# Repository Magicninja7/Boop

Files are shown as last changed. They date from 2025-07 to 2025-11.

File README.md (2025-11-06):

Description: Its a polar, 4axis, cantivileerian 3d printer! It uses a unorthodox aproach to rotate the hotend in b axis, and y axis, using only 2 motors and being pretty cool! The printbed is also backlit!! :3
WHy? idk, felt like it tbh. Saw a cool video on yt, thought: i wanna do that. And then highway happened. And then this happened.

## Cad 
looks kinda sick ngl

## PCB
this took more time than you think

## Diagram

Power Supply (LRS-350-24) Connections

LRS-350-24:

    AC Input L (Live): → Mains AC Hot
    AC Input N (Neutral): → Mains AC Neutral
    AC Input Ground: → Mains AC Ground
    +V (24V): → SKR3 VIN terminal
    -V (Ground): → SKR3 GND terminal
    +V (24V): → LED Strip positive terminal
    -V (Ground): → LED Strip negative terminal

SKR3 Main Board Connections
Stepper Motor Drivers

SKR3:

    Driver Socket X: → X-axis stepper driver (TMC2209/TMC2226)
    Driver Socket Y: → Y-axis stepper driver (TMC2209/TMC2226)
    Driver Socket Z: → Z-axis stepper driver (TMC2209/TMC2226)
    Driver Socket E0: → Extruder stepper driver (TMC2209/TMC2226)

Endstop Switches

SKR3:

    X-STOP pin 1 (Signal): → X endstop switch NO (Normally Open)
    X-STOP pin 2 (GND): → X endstop switch COM (Common)
    Y-STOP pin 1 (Signal): → Y endstop switch NO (Normally Open)
    Y-STOP pin 2 (GND): → Y endstop switch COM (Common)
    Z-STOP pin 1 (Signal): → Z endstop switch NO (Normally Open)
    Z-STOP pin 2 (GND): → Z endstop switch COM (Common)

Hotend (XC1) Connections

SKR3:

    HE0 pin 1 (+): → XC1 hotend heater cartridge positive
    HE0 pin 2 (-): → XC1 hotend heater cartridge negative
    TH0 pin 1 (Signal): → B57560G1104F000 thermistor pin 1
    TH0 pin 2 (GND): → B57560G1104F000 thermistor pin 2
    FAN0 pin 1 (+): → XC1 cooling fan positive (24V)
    FAN0 pin 2 (-): → XC1 cooling fan negative

Print Bed Connections

SKR3:

    HE1/BED pin 1 (+): → Print bed heater positive
    HE1/BED pin 2 (-): → Print bed heater negative
    THB pin 1 (Signal): → Bed thermistor positive (if separate)
    THB pin 2 (GND): → Bed thermistor negative (if separate)

LED Strip Connections

SKR3:

    FAN1 pin 1 (+): → LED strip positive (via MOSFET if needed)
    FAN1 pin 2 (-): → LED strip negative

## Parts

| Part | Qty | total$ | link |
| ---- | --- | ----- | ---- |
| sherpa mini | 1 | 24 | [Ali](https://pl.aliexpress.com/item/1005002487727392.html?gatewayAdapt=glo2pol) |
| vslot rail | 2 | 16 | [Ali](https://pl.aliexpress.com/i/1005003311298946.html?gatewayAdapt=glo2pol)
| nema17+screw | 2 | 20 | [Ali](https://pl.aliexpress.com/item/1005005575285492.html?gatewayAdapt=usa2pol)
| nema17 | 3 | 15 | [Ali](https://pl.aliexpress.com/item/1005003874936862.html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)
| skr3+drivers | 1 | 77 | [Ali](https://www.aliexpress.com/item/1005007540045155.html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)
| lrs-350-24 | 1 | 35 | [Ali](https://www.aliexpress.com/item/1005006104414563.html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)
| pillow-bearing | 2 | 12 | [Ali](https://pl.aliexpress.com/item/1005008115694493.html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)
| pulley | 2 | 3 | [Ali](https://www.aliexpress.us/item/1005004314084512.html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)
| pulley no-teeth | 4 | 12 | [Ali](https://www.aliexpress.us/item/1005004314084512.html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)
| back-pulley-xaxis | 1 | 2 | [Ali](https://www.aliexpress.us/item/32817328238.html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)
| big-xaxis-pulley | 1 | 5 | [Ali](https://www.fallshaw.com.au/products/SPBRGQ6004X20)
| bearing-uni | 4 | 5 | [Ali](https://modelemax.pl/en/bearings/19394-ball-bearing-8-24-8mm-628zz)
| gantry_vslot | 2 | 18 | [Ali](https://pl.aliexpress.com/item/4000252044823.html?gatewayAdapt=glo2pol)
| 4010 fan | 1 | 4 | [Ali](https://pl.aliexpress.com/item/1005003462239029.html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)
| sliding rod | 1 | 3.2 | [ali](https://pl.aliexpress.com/item/1005006293171727.html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)
| lm8uu bearing | 2 | 3 | [ali](https://pl.aliexpress.com/item/1005007070280422.html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)
| m4 screws+nuts | 36 | 8 | local_shop
| m3 screws+nuts | 25 | 8 | local_shop
| m2 wcrews+nutss | 4 | 1 | local_shop
| m2.5 screw | 2 | 1 | local_shop
| m5 screws+nuts | 35 | 4 | local_shop
| m8 screws+nuts | 5 | 4 | local_shop
| B57560G1104F000 thermistor | 2 | 8 | [mouser](https://eu.mouser.com/ProductDetail/EPCOS-TDK/B57560G1104F000?qs=%2FsLciWRBLmAyaJsNOAuWiw%3D%3D)
| leds4printbed | 75 | 15 | [piekarz🔥](https://www.piekarz.pl/37911-dioda-led-worldsemi-ws2812b-v4/)
| gt2 belt | 1 | 8 | [Ali](https://www.aliexpress.us/item/10000115962505.html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)
| nutblock | 2 | 6 | [Ali](https://pl.aliexpress.com/item/1005004033091930.html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) 
| xc1 hotend | 1 | 2 | [Ali](https://pl.aliexpress.com/item/1005007319888761.html)
| jumper cables (m2m & f2f & m2f) | 40 each | 8 | [Botland](https://botland.com.pl/przewody-polaczeniowe-zensko-meskie/19621-zestaw-przewodow-polaczeniowych-justpi-zensko-meskie-20cm-40szt-5903351243025.html) note: after customs aliexpress is actually more expensive + m2m and f2f connectors cost the same - ~2.5$)
| endstop switches | 3 | 4 | [ali](https://pl.aliexpress.com/item/1005008640444653.html)  
| pcb | 1 | 20 | [jlcpcb](https://jlcpcb.com/)

holy fuck 
its actually exactly 350$ 
wtf
nicee
i though i was gonna pay from pocket

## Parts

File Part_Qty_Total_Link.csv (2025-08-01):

Part | Qty | Total | Link
sherpa mini | 1 | 34 | https://pl.aliexpress.com/item/1005002487727392.html
vslot rail | 2 | 16 | https://pl.aliexpress.com/i/1005003311298946.html?gatewayAdapt=glo2pol
nema17+screw | 1 | 50 | https://www.aliexpress.us/item/1005005575285492.html?mp=1&gatewayAdapt=glo2usa
nema17 | 3 | 44 | https://www.aliexpress.us/item/1005007721263858.html?pdp
skr3+drivers | 1 | 77 | https://www.aliexpress.com/item/1005007540045155.html
lrs-350-24 | 1 | 35 | https://www.aliexpress.com/item/1005006104414563.html
pillow-bearing | 2 | 12 | https://pl.aliexpress.com/item/1005008115694493.html?pd
pulley | 2 | 3 | https://www.aliexpress.us/item/1005004314084512.html
pulley no-teeth | 4 | 12 | https://www.aliexpress.us/item/1005004314084512.html
back-pulley-xaxis | 1 | 2 | https://www.aliexpress.us/item/32817328238.html
big-xaxis-pulley | 1 | 5 | https://www.fallshaw.com.au/products/SPBRGQ6004X20
bearing-uni | 4 | 5 | https://modelemax.pl/en/bearings/19394-ball-bearing-8-24-8mm-628zz
gantry_vslot | 2 | 18 | https://pl.aliexpress.com/item/4000252044823.html?gatewayAdapt=glo2pol
4010 fan | 1 | 4 | https://pl.aliexpress.com/item/1005003462239029.html?pdp_ext_f
sliding rod | 1 | 23 | https://pl.aliexpress.com/item/1005006293171727.html?pdp_e
lm8uu bearing | 2 | 3 | https://pl.aliexpress.com/item/1005007070280422.html
m4 screws+nuts | 36 | 8 | local_shop
m3 screws+nuts | 25 | 8 | local_shop
m2 wcrews+nutss | 4 | 1 | local_shop
m2.5 screw | 2 | 1 | local_shop
m5 screws+nuts | 35 | 4 | local_shop
m8 screws+nuts | 5 | 4 | local_shop
B57560G1104F000 thermistor | 2 | 8 | https://eu.mouser.com/ProductDetail/EPCOS-TDK/B57560G1104F000?qs=%2FsLciWRBLmAyaJsNOAuWiw%3D%3D
leds4printbed | 75 | 15 | https://www.piekarz.pl/37911-dioda-led-worldsemi-ws2812b-v4/
gt2 belt | 1 | 8 | https://www.aliexpress.us/item/10000115962505.html?pdp_
nutblock | 2 | 6 | https://pl.aliexpress.com/item/1005004033091930.html?pdp_ext_
xc1 hotend | 1 | 2 | https://pl.aliexpress.com/item/1005007319888761.html
jumper cables (m2m & f2f & m2f) | 40 each | 8 | https://botland.com.pl/przewody-polaczeniowe-zensko-meskie/19621-zestaw-przewodow-polaczeniowych-justpi-zensko-meskie-20cm-40szt-590335
endstop switches | 3 | 4 | https://pl.aliexpress.com/item/1005008640444653.html
pcb | 1 | 50 | https://jlcpcb.com/

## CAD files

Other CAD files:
Main_v58.f3z

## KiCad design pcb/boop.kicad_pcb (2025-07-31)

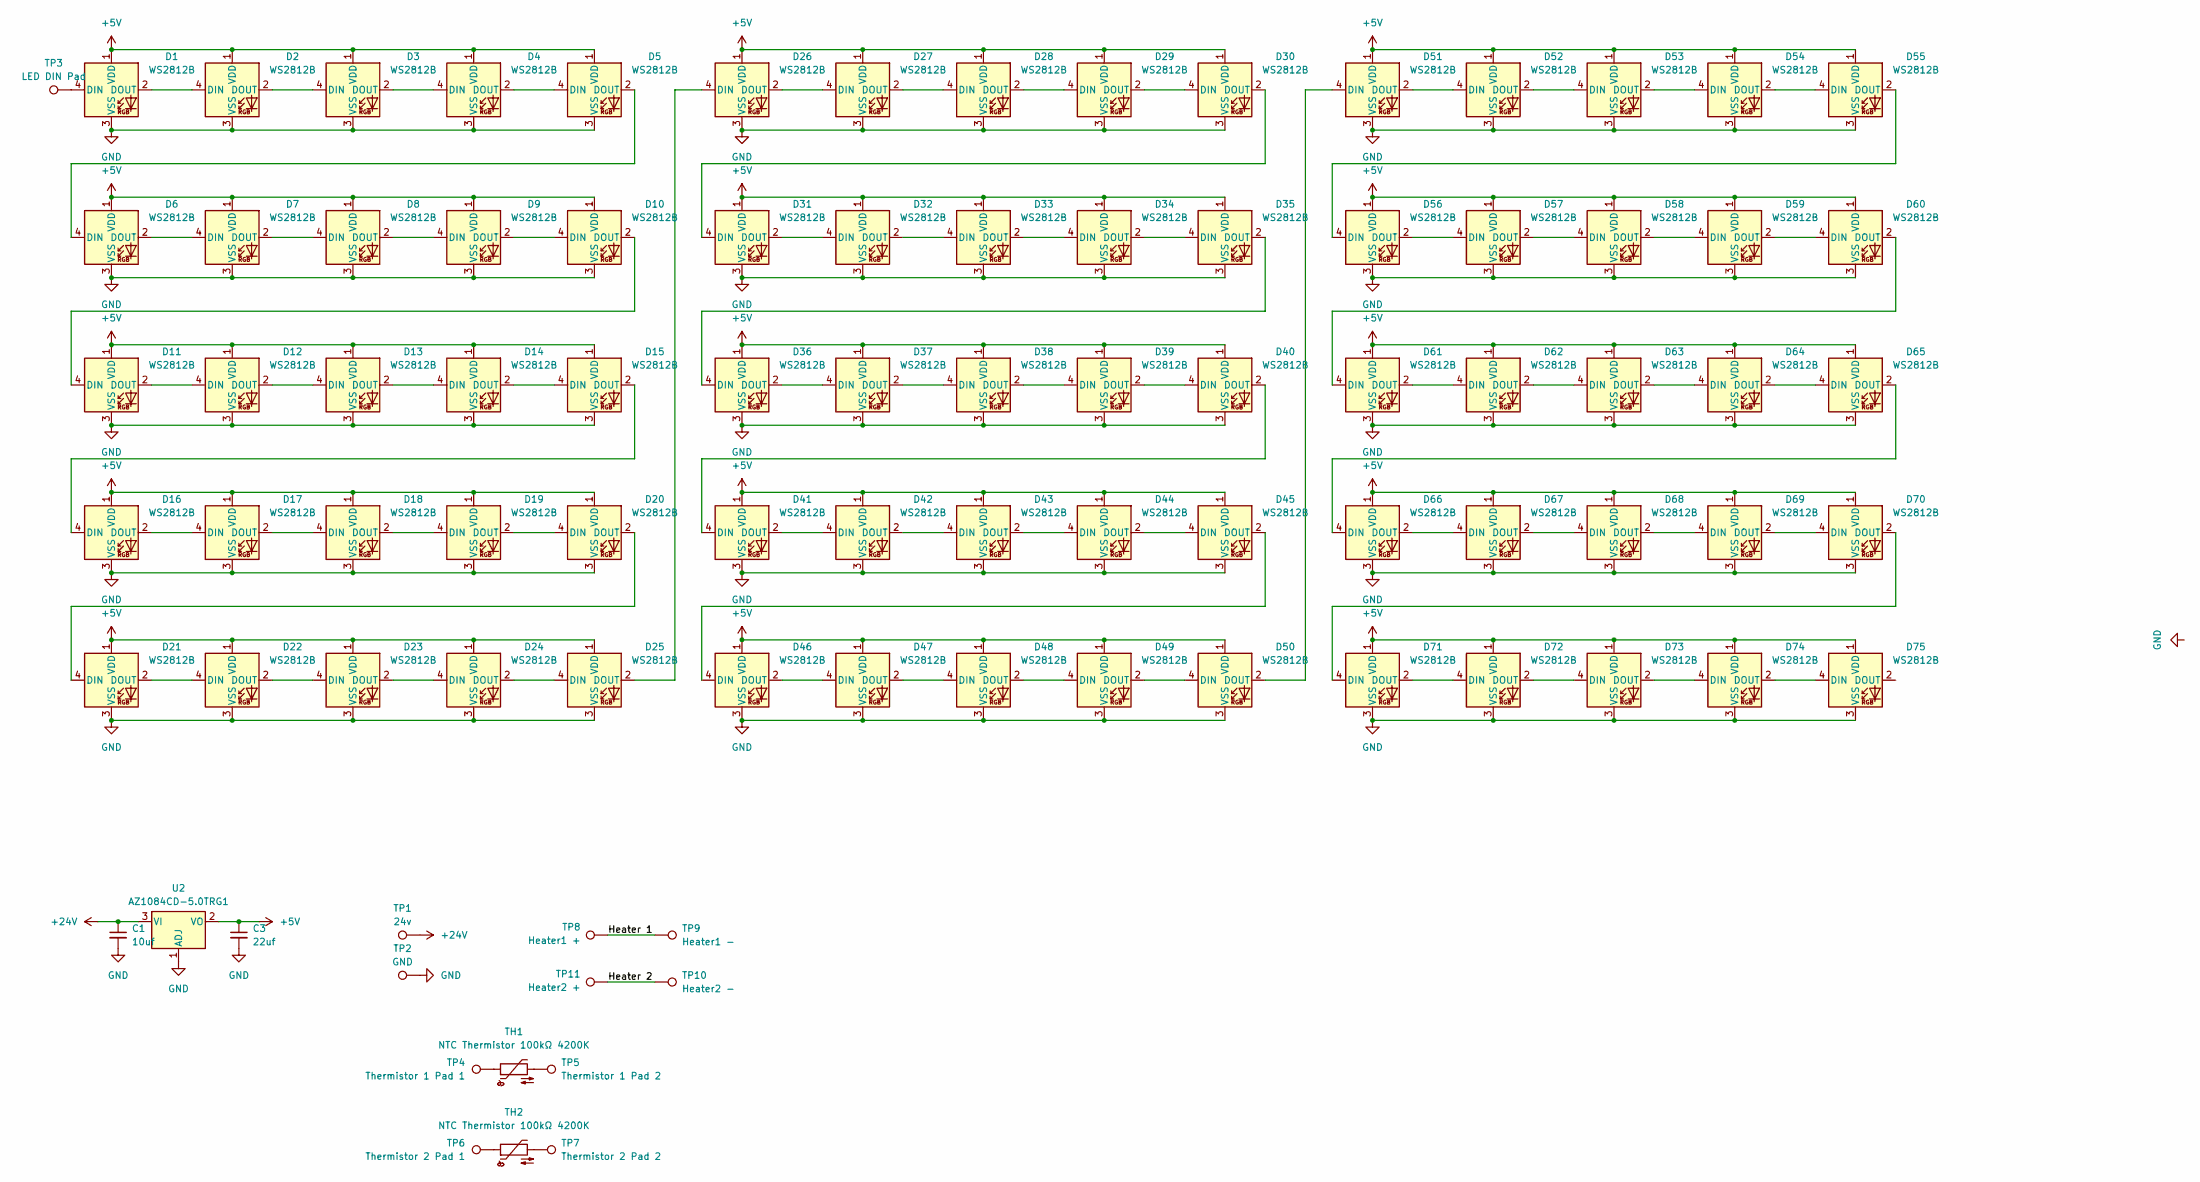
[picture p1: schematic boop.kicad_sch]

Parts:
C1: 10uf
C3: 22uf
D1, D2, D3, D4, D5, D6, D7, D8, D9, D10, D11, D12, D13, D14, D15, D16, D17, D18, D19, D20, D21, D22, D23, D24, D25, D26, D27, D28, D29, D30, D31, D32, D33, D34, D35, D36, D37, D38, D39, D40, D41, D42, D43, D44, D45, D46, D47, D48, D49, D50, D51, D52, D53, D54, D55, D56, D57, D58, D59, D60, D61, D62, D63, D64, D65, D66, D67, D68, D69, D70, D71, D72, D73, D74, D75: WS2812B; LED_WS2812B_PLCC4_5.0x5.0mm_P3.2mm
TH1, TH2: NTC Thermistor 100kΩ 4200K; R_0805_2012Metric_Pad1.20x1.40mm_HandSolder
TP1: 24v; TestPoint_Pad_4.0x4.0mm
TP2: GND; TestPoint_Pad_4.0x4.0mm
TP3: LED DIN Pad; TestPoint_Pad_2.5x2.5mm
TP4: Thermistor 1 Pad 1; TestPoint_Pad_2.0x2.0mm
TP5: Thermistor 1 Pad 2; TestPoint_Pad_2.0x2.0mm
TP6: Thermistor 2 Pad 1; TestPoint_Pad_2.0x2.0mm
TP7: Thermistor 2 Pad 2; TestPoint_Pad_2.0x2.0mm
TP8: Heater1 +; TestPoint_Pad_4.0x4.0mm
TP9: Heater1 -; TestPoint_Pad_4.0x4.0mm
TP10: Heater2 -; TestPoint_Pad_4.0x4.0mm
TP11: Heater2 +; TestPoint_Pad_4.0x4.0mm
U2: AZ1084CD-5.0TRG1; TO-252-2

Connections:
+5V: C3.1, D1.1 (VDD), D2.1 (VDD), D3.1 (VDD), D4.1 (VDD), D5.1 (VDD), D6.1 (VDD), D7.1 (VDD), D8.1 (VDD), D9.1 (VDD), D10.1 (VDD), D11.1 (VDD), D12.1 (VDD), D13.1 (VDD), D14.1 (VDD), D15.1 (VDD), D16.1 (VDD), D17.1 (VDD), D18.1 (VDD), D19.1 (VDD), D20.1 (VDD), D21.1 (VDD), D22.1 (VDD), D23.1 (VDD), D24.1 (VDD), D25.1 (VDD), D26.1 (VDD), D27.1 (VDD), D28.1 (VDD), D29.1 (VDD), D30.1 (VDD), D31.1 (VDD), D32.1 (VDD), D33.1 (VDD), D34.1 (VDD), D35.1 (VDD), D36.1 (VDD), D37.1 (VDD), D38.1 (VDD), D39.1 (VDD), D40.1 (VDD), D41.1 (VDD), D42.1 (VDD), D43.1 (VDD), D44.1 (VDD), D45.1 (VDD), D46.1 (VDD), D47.1 (VDD), D48.1 (VDD), D49.1 (VDD), D50.1 (VDD), D51.1 (VDD), D52.1 (VDD), D53.1 (VDD), D54.1 (VDD), D55.1 (VDD), D56.1 (VDD), D57.1 (VDD), D58.1 (VDD), D59.1 (VDD), D60.1 (VDD), D61.1 (VDD), D62.1 (VDD), D63.1 (VDD), D64.1 (VDD), D65.1 (VDD), D66.1 (VDD), D67.1 (VDD), D68.1 (VDD), D69.1 (VDD), D70.1 (VDD), D71.1 (VDD), D72.1 (VDD), D73.1 (VDD), D74.1 (VDD), D75.1 (VDD), U2.2 (VO)
+24V: C1.1, TP1.1, U2.3 (VI)
/Heater 1: TP8.1, TP9.1
/Heater 2: TP10.1, TP11.1
GND: C1.2, C3.2, D1.3 (VSS), D2.3 (VSS), D3.3 (VSS), D4.3 (VSS), D5.3 (VSS), D6.3 (VSS), D7.3 (VSS), D8.3 (VSS), D9.3 (VSS), D10.3 (VSS), D11.3 (VSS), D12.3 (VSS), D13.3 (VSS), D14.3 (VSS), D15.3 (VSS), D16.3 (VSS), D17.3 (VSS), D18.3 (VSS), D19.3 (VSS), D20.3 (VSS), D21.3 (VSS), D22.3 (VSS), D23.3 (VSS), D24.3 (VSS), D25.3 (VSS), D26.3 (VSS), D27.3 (VSS), D28.3 (VSS), D29.3 (VSS), D30.3 (VSS), D31.3 (VSS), D32.3 (VSS), D33.3 (VSS), D34.3 (VSS), D35.3 (VSS), D36.3 (VSS), D37.3 (VSS), D38.3 (VSS), D39.3 (VSS), D40.3 (VSS), D41.3 (VSS), D42.3 (VSS), D43.3 (VSS), D44.3 (VSS), D45.3 (VSS), D46.3 (VSS), D47.3 (VSS), D48.3 (VSS), D49.3 (VSS), D50.3 (VSS), D51.3 (VSS), D52.3 (VSS), D53.3 (VSS), D54.3 (VSS), D55.3 (VSS), D56.3 (VSS), D57.3 (VSS), D58.3 (VSS), D59.3 (VSS), D60.3 (VSS), D61.3 (VSS), D62.3 (VSS), D63.3 (VSS), D64.3 (VSS), D65.3 (VSS), D66.3 (VSS), D67.3 (VSS), D68.3 (VSS), D69.3 (VSS), D70.3 (VSS), D71.3 (VSS), D72.3 (VSS), D73.3 (VSS), D74.3 (VSS), D75.3 (VSS), TP2.1, U2.1 (ADJ)
unnamed: D1.4 (DIN), TP3.1
unnamed: D1.2 (DOUT), D2.4 (DIN)
unnamed: D2.2 (DOUT), D3.4 (DIN)
unnamed: D3.2 (DOUT), D4.4 (DIN)
unnamed: D4.2 (DOUT), D5.4 (DIN)
unnamed: D5.2 (DOUT), D6.4 (DIN)
unnamed: D6.2 (DOUT), D7.4 (DIN)
unnamed: D7.2 (DOUT), D8.4 (DIN)
unnamed: D8.2 (DOUT), D9.4 (DIN)
unnamed: D9.2 (DOUT), D10.4 (DIN)
unnamed: D10.2 (DOUT), D11.4 (DIN)
unnamed: D11.2 (DOUT), D12.4 (DIN)
unnamed: D12.2 (DOUT), D13.4 (DIN)
unnamed: D13.2 (DOUT), D14.4 (DIN)
unnamed: D14.2 (DOUT), D15.4 (DIN)
unnamed: D15.2 (DOUT), D16.4 (DIN)
unnamed: D16.2 (DOUT), D17.4 (DIN)
unnamed: D17.2 (DOUT), D18.4 (DIN)
unnamed: D18.2 (DOUT), D19.4 (DIN)
unnamed: D19.2 (DOUT), D20.4 (DIN)
unnamed: D20.2 (DOUT), D21.4 (DIN)
unnamed: D21.2 (DOUT), D22.4 (DIN)
unnamed: D22.2 (DOUT), D23.4 (DIN)
unnamed: D23.2 (DOUT), D24.4 (DIN)
unnamed: D24.2 (DOUT), D25.4 (DIN)
unnamed: D25.2 (DOUT), D26.4 (DIN)
unnamed: D26.2 (DOUT), D27.4 (DIN)
unnamed: D27.2 (DOUT), D28.4 (DIN)
unnamed: D28.2 (DOUT), D29.4 (DIN)
unnamed: D29.2 (DOUT), D30.4 (DIN)
unnamed: D30.2 (DOUT), D31.4 (DIN)
unnamed: D31.2 (DOUT), D32.4 (DIN)
unnamed: D32.2 (DOUT), D33.4 (DIN)
unnamed: D33.2 (DOUT), D34.4 (DIN)
unnamed: D34.2 (DOUT), D35.4 (DIN)
unnamed: D35.2 (DOUT), D36.4 (DIN)
unnamed: D36.2 (DOUT), D37.4 (DIN)
unnamed: D37.2 (DOUT), D38.4 (DIN)
unnamed: D38.2 (DOUT), D39.4 (DIN)
unnamed: D39.2 (DOUT), D40.4 (DIN)
unnamed: D40.2 (DOUT), D41.4 (DIN)
unnamed: D41.2 (DOUT), D42.4 (DIN)
unnamed: D42.2 (DOUT), D43.4 (DIN)
unnamed: D43.2 (DOUT), D44.4 (DIN)
unnamed: D44.2 (DOUT), D45.4 (DIN)
unnamed: D45.2 (DOUT), D46.4 (DIN)
unnamed: D46.2 (DOUT), D47.4 (DIN)
unnamed: D47.2 (DOUT), D48.4 (DIN)
unnamed: D48.2 (DOUT), D49.4 (DIN)
unnamed: D49.2 (DOUT), D50.4 (DIN)
unnamed: D50.2 (DOUT), D51.4 (DIN)
unnamed: D51.2 (DOUT), D52.4 (DIN)
unnamed: D52.2 (DOUT), D53.4 (DIN)
unnamed: D53.2 (DOUT), D54.4 (DIN)
unnamed: D54.2 (DOUT), D55.4 (DIN)
unnamed: D55.2 (DOUT), D56.4 (DIN)
unnamed: D56.2 (DOUT), D57.4 (DIN)
unnamed: D57.2 (DOUT), D58.4 (DIN)
unnamed: D58.2 (DOUT), D59.4 (DIN)
unnamed: D59.2 (DOUT), D60.4 (DIN)
unnamed: D60.2 (DOUT), D61.4 (DIN)
unnamed: D61.2 (DOUT), D62.4 (DIN)
unnamed: D62.2 (DOUT), D63.4 (DIN)
unnamed: D63.2 (DOUT), D64.4 (DIN)
unnamed: D64.2 (DOUT), D65.4 (DIN)
unnamed: D65.2 (DOUT), D66.4 (DIN)
unnamed: D66.2 (DOUT), D67.4 (DIN)
unnamed: D67.2 (DOUT), D68.4 (DIN)
unnamed: D68.2 (DOUT), D69.4 (DIN)
unnamed: D69.2 (DOUT), D70.4 (DIN)
unnamed: D70.2 (DOUT), D71.4 (DIN)
unnamed: D71.2 (DOUT), D72.4 (DIN)
unnamed: D72.2 (DOUT), D73.4 (DIN)
unnamed: D73.2 (DOUT), D74.4 (DIN)
unnamed: D74.2 (DOUT), D75.4 (DIN)
unnamed: TH1.1, TP4.1
unnamed: TH1.2, TP5.1
unnamed: TH2.1, TP6.1
unnamed: TH2.2, TP7.1

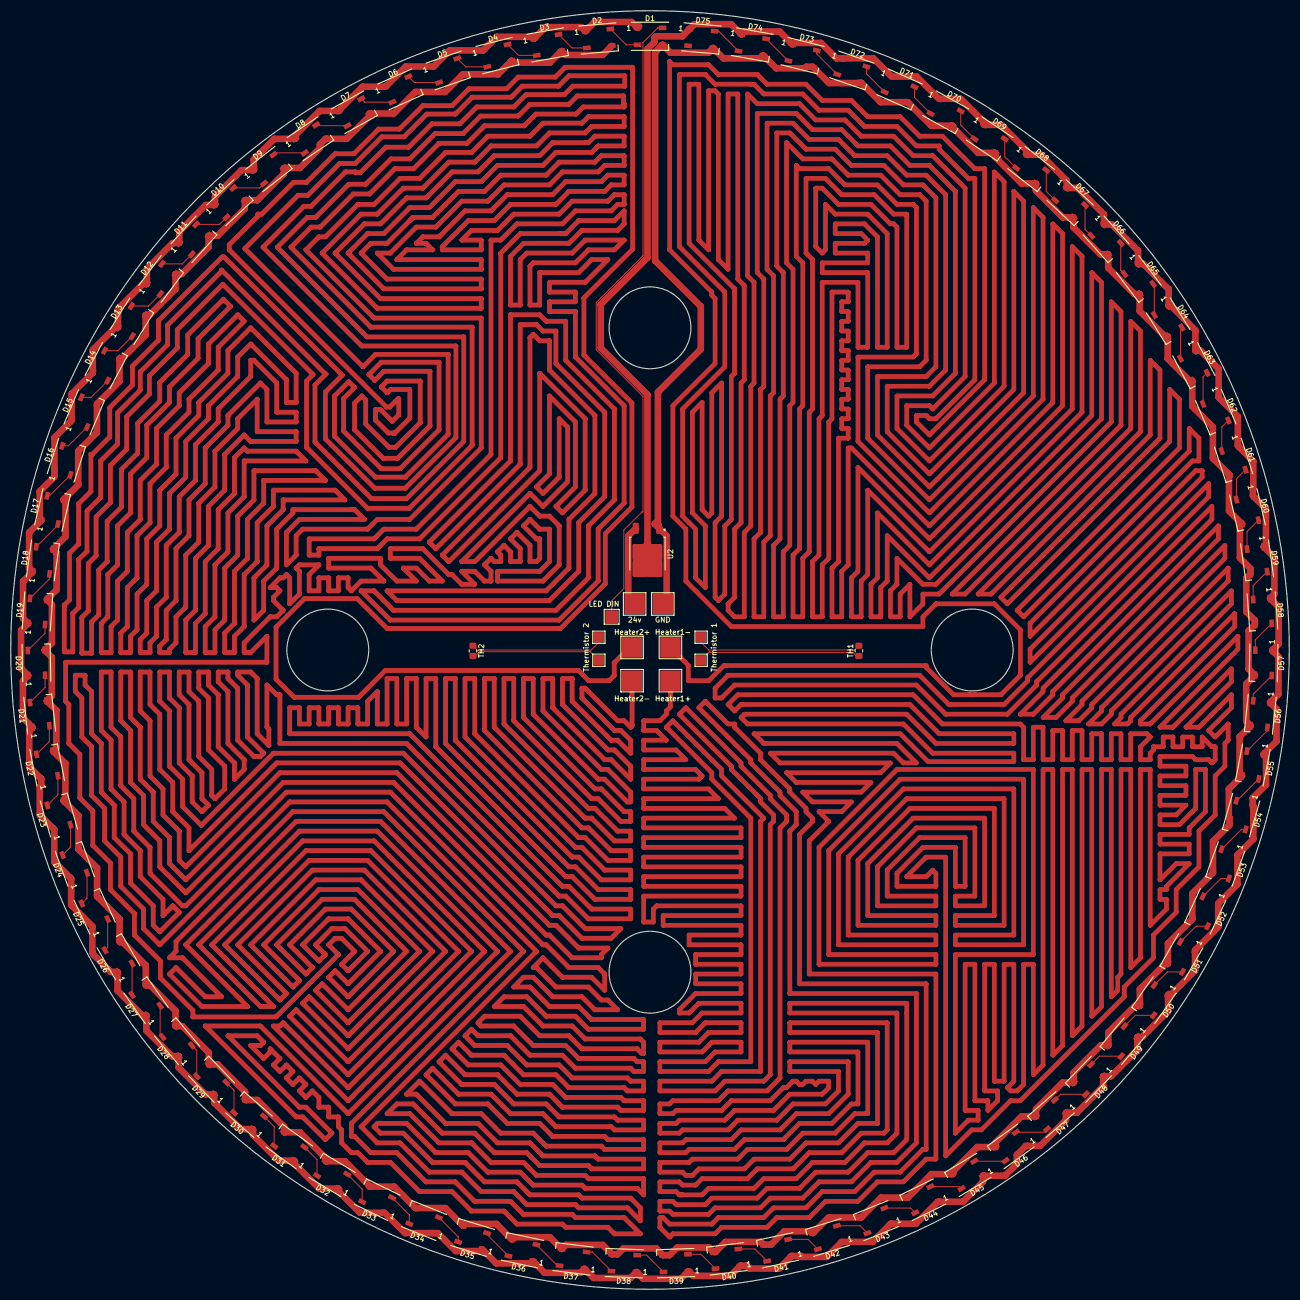
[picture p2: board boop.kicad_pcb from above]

Board: 2 copper layers, 250.0 x 250.0 mm, 89 parts (0 on the bottom side), 84 nets.

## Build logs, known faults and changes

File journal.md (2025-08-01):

This is a devlog for this 3d printer im making!
(im keeping this casual)

total time: 98.5 hours

# Day 0 (24-25.05.25) ~15 hours
Today i did research, setup fusion, and started making a scetch for the base!
After that, i started making the polar mechanism itself, designing the gears and belt. Now if gear A (the small one) is spun, gear B spins too. On the left, seperated for now, is a part of the printbed and elemesnts allowing it to spin (atleast they will in the future).
spinny_gears

# Day 1 & 2 (27 & 29.05.2025) ~2.5 hours
With exams, i didn't have time to do much. I did do one thing though, draw out the design on my whiteboard. I also found a good extruder to use (sherpa mini), paired with the XC1 hotend and a dragon burner. I have already gotten the cads for them, and only need to assemble them within fusion.
And more research on how to do the z axis. The problem with the design in the video, is that it shakes, and like a lot. To solve it, im considering adding another arm, on the other side of the cartridge. This would substantially minimalise shaking, but slightly increase the price. I think its a good trade, as the other way involves getting rid on the cantileverian design.

# Day 3 (13.06.2025) ~0 hours lmao
Thank god i passed everything, finally have got time to continue this project. 

# Day 4 (20.06.2025) ~3 hours
I completed the whole extruder part, by using the sherpa mini with the xc1 hotend, combined with the dragon burner. Starting on the x axis, i have completed the design on paper, now i only need to bring it onto fusion. I also will be using a 2x sliding rods, and 2x lead screws for the y axis, but i will add that after i finish the x axis.
making x axis

# Day 5 (21.06.2025) ~5 hours
Im continuing my work on the x axis. Found and added pulleys needed for the design (6 total), added the vrail and carriage). All designed by me, its why it took soo long
carriage

# Day 6 (25.06.2025) ~6 hours
Today i added a pulley at the end of the vrail (it isnt connected yet tho, im yet to do that). I also added a second pulley at the other end, it will be moving the extruder. In here, i created a part that will hold it, it fit snugggly into the vrail, with 0.1mm margin. It also will have a whole in the middle (through the whole thing, including the vrail), to slide in a blot, so the whole thing doesnt move or shake. It also has 2 ball bearings, with inside diamater of 20mm, the same as the pulley.
wroom
up!

# Day 7 (26.06.2025) ~5 hours
I added the holder for the bottom pulley, and redid the holder for the front pulley (it had 0 margin, and not it has 0.05 margin. Idk if its the gap is big enough, but its a cheap 3d printed part, so no big deal). I also did research on how exactly a mount should look, since i need one to connect my sherpa with xc1. I decided on the 4010 axial to provide general flow onto the heatsink, and a radial fan (5015) for the tip of the nozzle. I will want to make it as light as possible, but will likely need an airduct to channel the air, but since its plastic it shouldnt add much.
the rail n carriage n pulley

# Day 8 (26-27.06.2025) ~6 hours
I created the mount, connecting the 4010 fan, with the sherpa and hotend. The blank space opposite of the fan, will be filled by a material mesh i have at home. It currently doesnt have a mount, since i plan to add another part, made with cnc, or bought online, where i will insert the 20mm diamater rod, and then screw it to the mount.
fan view
other view

# Day 9 (03.06.2025) ~5 hours
I made a mount, however its horrible. takes up too much space.
mount

Now it looks like this! It has a space to screw it in, on its 4 corners, and a screw to fit into the rod, which is also custom made!
mount_only

I also atlast connected it to the rod, and the x axis is completed!
whole thing

# Day 10 (06.06.2025) ~8 hours
Now i added a belt and created new pulleys for the x axis!
belt
I has to redo the belt, bc i needed to increase the length of the xaxis rail by 100mm. I also added 2 plates on either side, to hold all the pulleys, and positioned the nut blocks, made screw holes for it. Also put the nema17 motors, but theyre not yet mounted.
flippy flippy flap flap

# Day 11 (07.07.2025) ~4 hours
Today i added holders for both sides of the xaxis, which hold everything together. And put the nema17 stepper motors for 2 pulleys, and 2 lead screwws they'll be powering. I have decided on putting both on one side, since putting 1 per side would make it extremely akward to design, and would unevenly distribute weight in a way thats harder to fix (now, i can just put weights/needed electronics in the other side). The heavier side also has a linear rail.
left pic
right pic

# Day 12 (08.07.2025) ~4 hours
Now i added holders for the 3 stepper motors on the bottom, and added a holder for thr rail. I also started the protectors for the screws, and recreated a pillow bearing. Its still a wip, but i need only to add the top, reinforce it, and connect it to the linear rail holder.
side
bottom

# Day 13/14  (09.07.2025 - 21.07.2025) ~10 hours
This 2 weeks i added classic rail, to stabilise the build, as well as adding 3d-printable supports for it. The rail one, is connected to the screw one, and those are connected to the nema17 holder at the base, and to the other linear screw holder at the top.
left profil
right profil
And i also upgraded the holders for the 2 nema17 i have at the bottom, now its 1 3dprintable part for both motors, which o directly screwed to the base in 8 places, connected to the linear screw and classic rail holders, via screws, and is held in place by an additional metal plate, at its top. I also added the whole base and space in the middle for parts such as: control board, psu, stepper drivers, cable managment, etc.
plate

# Day 15 (25.07.2025) ~8 hours
A lot of stuff done today!
it looks like this now! I added a sliding rod on the opposite side if the x axis, relative to the classic rail. Now, it will definitely be stable, so to not make it ugly, i added a few cutouts on the plate! Said plate is connected to the sliding rod, via 2 adapters and LM8uu bearings. 
On the other side, i completely revamped the printbet, now its more stable, slimmer, and cheaper. The gear holding the belt, is connected to the printbed. It uses 1 bearing with 29mm inside radius, which is used to insert a static rod from the base. The base was also modernised.







# Day 16 (30-31.07.2025) ~8 hours
The first part of making this (the schematic and wiring leds) was a pain, but wiring the heating pads was weirdly satisfying, like the slime videos xd. 
The pixels are for pure decorational purposes, and the wiring was made to keep almost all of the printbed evenly heated, even if its asymetrical.
wire

# Day 17 (31.07.2025 the evening, not 3am like before :3) ~9 hours
Turns out making reprap firmware at the last possible day wasn't the best idea, but thankfully i did my research and ytvideo watching earlier, so it went rather quick.
f this who even made this bs lang it makes no sense if it werent for tutorials id be fucked

Parts:

| Part | Qty | total | link |
| ---- | --- | ----- | ---- |
| sherpa mini | 1 | 34 | [Ali](https://pl.aliexpress.com/item/1005002487727392.html) |
| vslot rail | 2 | 16 | [Ali](https://pl.aliexpress.com/i/1005003311298946.html?gatewayAdapt=glo2pol)
| nema17+screw | 1 | 50 | [Ali](https://www.aliexpress.us/item/1005005575285492.html?mp=1&gatewayAdapt=glo2usa)
| nema17 | 3 | 44 | [Ali](https://www.aliexpress.us/item/1005007721263858.html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)
| skr3+drivers | 1 | 77 | [Ali](https://www.aliexpress.com/item/1005007540045155.html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)
| lrs-350-24 | 1 | 35 | [Ali](https://www.aliexpress.com/item/1005006104414563.html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)
| pillow-bearing | 2 | 12 | [Ali](https://pl.aliexpress.com/item/1005008115694493.html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)
| pulley | 2 | 3 | [Ali](https://www.aliexpress.us/item/1005004314084512.html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)
| pulley no-teeth | 4 | 12 | [Ali](https://www.aliexpress.us/item/1005004314084512.html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)
| back-pulley-xaxis | 1 | 2 | [Ali](https://www.aliexpress.us/item/32817328238.html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)
| big-xaxis-pulley | 1 | 5 | [Ali](https://www.fallshaw.com.au/products/SPBRGQ6004X20)
| bearing-uni | 4 | 5 | [Ali](https://modelemax.pl/en/bearings/19394-ball-bearing-8-24-8mm-628zz)
| gantry_vslot | 2 | 18 | [Ali](https://pl.aliexpress.com/item/4000252044823.html?gatewayAdapt=glo2pol)
| 4010 fan | 1 | 4 | [Ali](https://pl.aliexpress.com/item/1005003462239029.html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)
| sliding rod | 1 | 23 | [ali](https://pl.aliexpress.com/item/1005006293171727.html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)
| lm8uu bearing | 2 | 3 | [ali](https://pl.aliexpress.com/item/1005007070280422.html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)
| m4 screws+nuts | 36 | 8 | local_shop
| m3 screws+nuts | 25 | 8 | local_shop
| m2 wcrews+nutss | 4 | 1 | local_shop
| m2.5 screw | 2 | 1 | local_shop
| m5 screws+nuts | 35 | 4 | local_shop
| m8 screws+nuts | 5 | 4 | local_shop
| B57560G1104F000 thermistor | 2 | 8 | [mouser](https://eu.mouser.com/ProductDetail/EPCOS-TDK/B57560G1104F000?qs=%2FsLciWRBLmAyaJsNOAuWiw%3D%3D)
| leds4printbed | 75 | 15 | [piekarz🔥](https://www.piekarz.pl/37911-dioda-led-worldsemi-ws2812b-v4/)
| gt2 belt | 1 | 8 | [Ali](https://www.aliexpress.us/item/10000115962505.html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)
| nutblock | 2 | 6 | [Ali](https://pl.aliexpress.com/item/1005004033091930.html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) 
| xc1 hotend | 1 | 2 | [Ali](https://pl.aliexpress.com/item/1005007319888761.html)
| jumper cables (m2m & f2f & m2f) | 40 each | 8 | [Botland](https://botland.com.pl/przewody-polaczeniowe-zensko-meskie/19621-zestaw-przewodow-polaczeniowych-justpi-zensko-meskie-20cm-40szt-5903351243025.html) note: after customs aliexpress is actually more expensive + m2m and f2f connectors cost the same - ~2.5$)
| endstop switches | 3 | 4 | ali  
| pcb | 1 | 50 | [jlcpcb](https://jlcpcb.com/)

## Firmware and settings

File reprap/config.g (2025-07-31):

global B_OFFSET = 0
global X_LENGTH = 115.5                      

G90                                           
M83                                             
M550 P"Boop"                                

M552 S1                                                    ; enable network
M586 P0 S1                                                 ; enable HTTP
M586 P1 S0                                                 ; disable FTP
M586 P2 S0                                                 ; disable Telnet

; Drives
M84 S30                                                    ; idle timeout

; commands  4 axis / polar config
M98 P"to4axis.g"

M915 B R0 F0 S-10                                                     
M915 X H100 R0 F0 S0                                                     


M955 P0 C"PB_2+PA_10" I46


; Z-Probe
M558 P5 C"^xstop" H5 F2000:500 T6000 A1                    ; Z switch and dive height + speed
G31 P500 X0 Y0 Z-8.5                                       ; Z probe trigger value, offset and trigger height

; Heaters
M140 H-1                                                   ; disable heatbed
M308 S0 P"e0temp" Y"thermistor" T100000 B4956 C1.587780e-7 ; config sensor as thermistor on pin e0temp
M950 H0 C"e0heat" T0                                       ; create nozzle heater output on e0heat and map to 0
M307 H0 R2.703 K0.364:0.000 D11.05 E1.35 S1.00 B0 V23.7    ; pwm config from autotune
M143 H0 S270                                               ; set temperature limit for heater 0 to 120C
M302 P1                                                    ; allow cold extrudes

; Fans
M950 F0 C"fan1"                                            ; create fan 0 on pin fan0 and set frequency
M106 P0 S0 H0 T50                                          ; set fan 0 value. Thermostatic control is turned on

M950 F1 C"!PA_7" Q50                                       ; create fan 1 on PA_0

; Tools
M563 P0 D0 F0 H0                                           ; define tool 0
G10 P0 X0 Y0 Z0                                            ; set tool 0 axis offsets
G10 P0 R0 S0                                               ; set initial tool 0 active and standby temperatures to 0C
T0                                                         ; select tool

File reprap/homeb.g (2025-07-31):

M400                  ; Wait for moves to finish
M913 X50 B50          ; drop motor current
M569 P1 V1            ; put driver 1 into stealth chop mode
M569 P2 V1            ; put driver 2 into stealth chop mode
M400
G91                   ; relative positioning
; G1 H2 Z10 F12000   ; lift Z relative to current position
G1 H2 X-10 B-10 F1000 ; go back a few mm
G1 H1 B1000 F200000   ; move quickly to X axis endstop and stop there (first pass)
G1 H0 B-90 F12000      ; go back a few mm
G1 H1 B1000 F200000   ; move slowly to X axis endstop once more (second pass)
; G1 H2 Z-10 F6000   ; lower Z again
G90                   ; absolute positioning
M400
M913 X100 B100        ; return current to 100%
M569 P1 V4000         ; put driver 1 into spread cycle mode
M569 P2 V4000         ; put driver 2 into spread cycle mode
M400
G1 B0 F12000
